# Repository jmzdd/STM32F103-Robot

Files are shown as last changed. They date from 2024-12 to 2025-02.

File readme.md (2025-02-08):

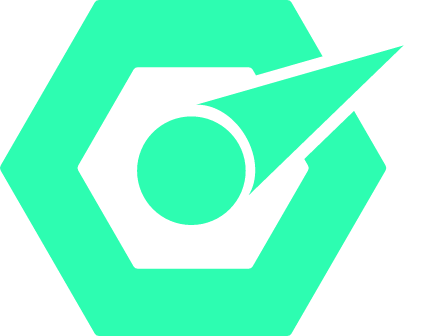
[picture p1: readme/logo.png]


# <p align="center">STM32F103-Robot</p>

<p align="center">
  
  
  
  
  
  
  
</p>

<p align="center" style="font-size: 24px; font-weight: bold;">🎉一个基于STM32F103C8T6的四足爬行机器人🎉</p>
<p align="center" style="font-size: 20px; font-weight: bold;">🚫项目仅供学习交流🚫</p>

## 一、项目介绍

&emsp;&emsp;本设计使用STM32F103C8T6作为主控，结合ESP32-CAM与MQTT，实现实时图像回传以及远程控制。

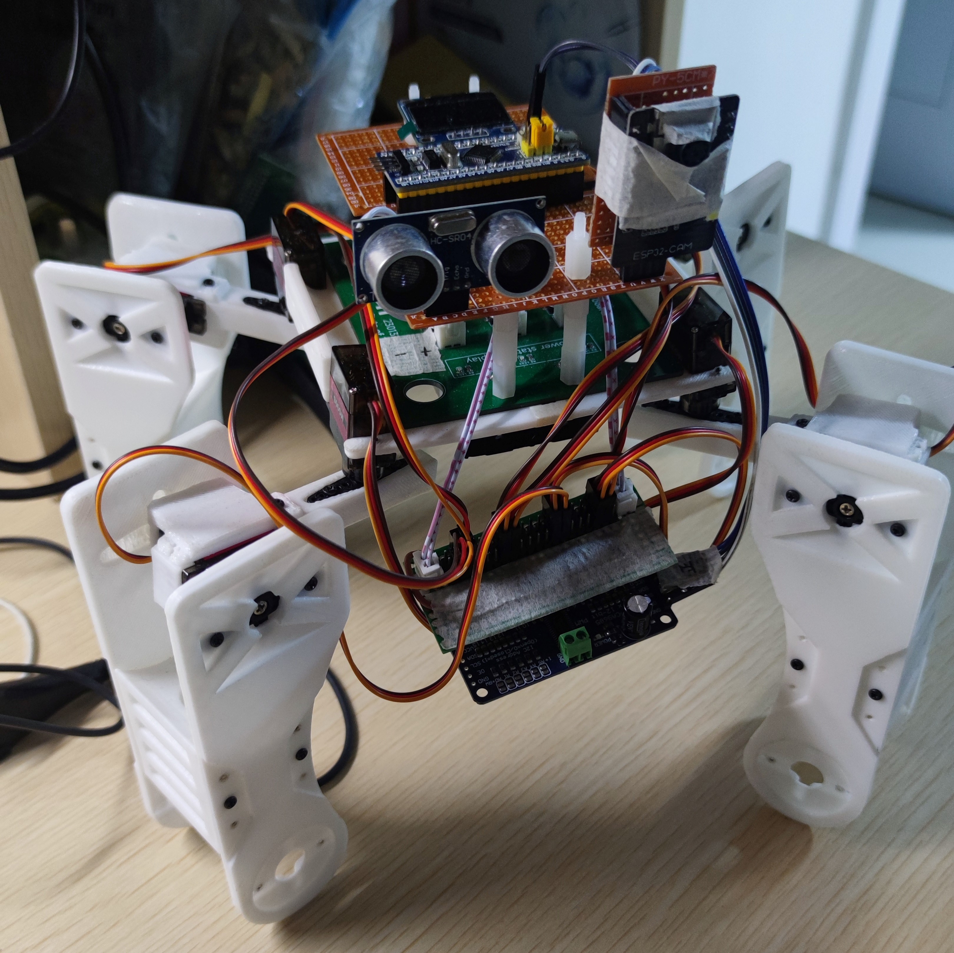
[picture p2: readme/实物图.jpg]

<p align="center">实物图</p>

&emsp;&emsp;在机器人的控制上使用了云端控制和本地控制两种方案。其中由Flet编写的移动端App能够通过MQTT协议与安装在服务器的EMQX进行通信，经云端传输的命令由ESP32-CAM接收后通过USART2传递给单片机，单片机就可以根据该命令控制模块，让机器人做出对应的动作。而ESP32-CAM拍摄的视频流则会实时上传至服务器，由服务器上部署的Nodejs Server接收后，通过网页呈现出来，至此实现了云端控制的全过程。

&emsp;&emsp;而本地控制则由Microdot来实现，在连接上由ESP32-CAM发出的热点之后，通过访问指定IP来访问本地控制面板。点击网页上的按钮就能够控制ESP32-CAM， ESP32-CAM通过串口向单片机发送命令。而由ESP32-CAM回传的图像流则会通过WIFI，实时显示在本地控制面板的上方。

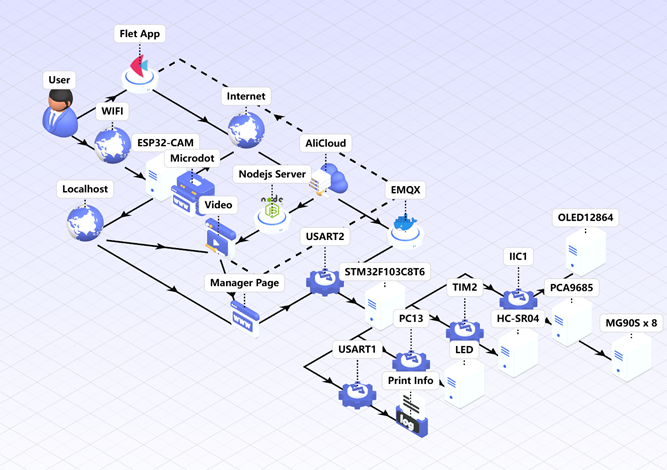
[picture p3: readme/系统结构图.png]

<p align="center">系统结构图</p>

&emsp;&emsp;仓库内包含了本项目所需的所有代码，其中还包括机器人的3D建模文件：

<div align="center">
  <table>
    <thead>
      <tr>
        <th style="text-align: left;">文件名</th>
        <th style="text-align: left;">说明</th>
      </tr>
    </thead>
    <tbody>
      <tr>
        <td style="text-align: left;">1、FreeCAD_Projects</td>
        <td style="text-align: left;">机器人3D建模工程文件</td>
      </tr>
      <tr>
        <td style="text-align: left;">2、HAL_C8T6</td>
        <td style="text-align: left;">开发STM32的工程文件</td>
      </tr>
      <tr>
        <td style="text-align: left;">3、Fletapp</td>
        <td style="text-align: left;">开发Flet应用的工程文件</td>
      </tr>
      <tr>
        <td style="text-align: left;">4、ESP32-CAM</td>
        <td style="text-align: left;">开发ESP32-CAM的Python代码以及前端代码</td>
      </tr>
      <tr>
        <td style="text-align: left;">5、CAM_Server</td>
        <td style="text-align: left;">服务器上负责ESP32-CAM图像接收的Nodejs代码</td>
      </tr>
      <tr>
        <td style="text-align: left;">6、Other</td>
        <td style="text-align: left;">包含Gerber文件和BOM表等文件</td>
      </tr>
    </tbody>
  </table>
</div>

## 二、项目设计过程

### 2.1 结构设计
&emsp;&emsp;四足爬行机器人的结构设计则使用了开源软件FreeCAD进行设计。结合MG90S舵机的尺寸，在腿部设计了凹槽与螺丝安装孔。机体中间预留电池安装孔，在关键位置还设计了螺丝孔，使结构更加牢固，方便后期的安装。

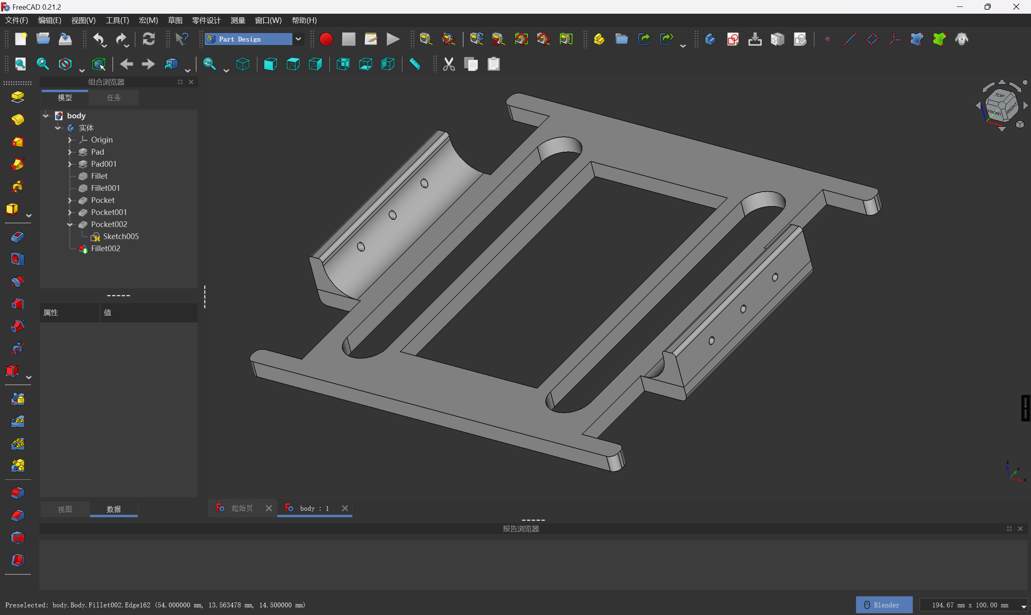
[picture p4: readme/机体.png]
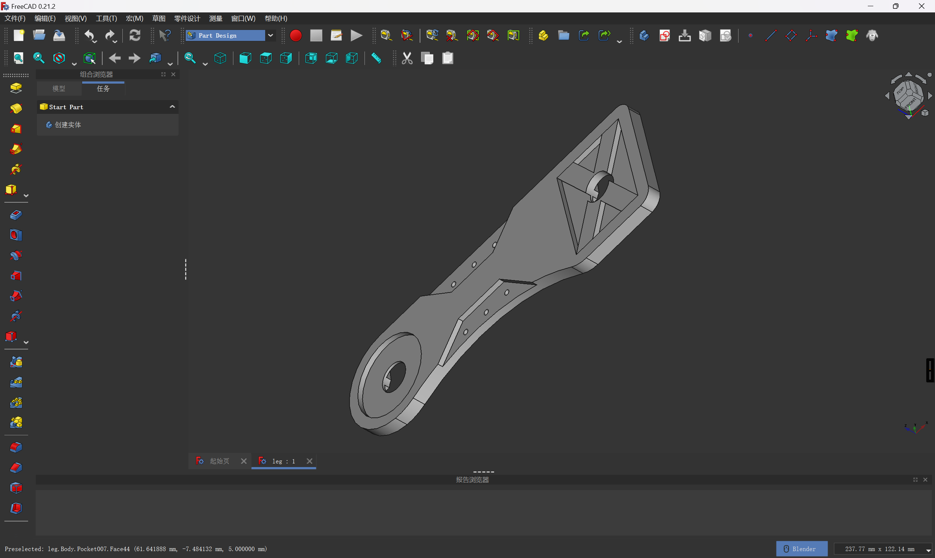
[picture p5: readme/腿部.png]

<p align="center">3D模型图</p>

&emsp;&emsp;建模完成后使用切片软件对模型进行切片，并将切片结果导入至3D打印机当中进行打印。填充密度为0.1mm，层厚0.2mm，挤出头温度设定为210℃。打印材料则选择了直径为1.75mm的PLA材料。电源板上预留了螺丝孔以安装尼龙柱，各个功能模块由万用板电路连接后通过尼龙柱堆叠在机体上方，方便快速装卸和调试。

### 2.2 电源设计

&emsp;&emsp;四足爬行机器人的电源模块选用了TI的TPS5430，在设计参考了[【电赛模块】TPS5430正负电源输出模块](https://oshwhub.com/quan-guo-dian-sai/dian-sai-mo-kuai-tps5430-fu-dian-yuan-shu-chu-mo-kuai)。电源模块上分别设计了三路电源，分别为舵机以及主控与功能模块进行供电。

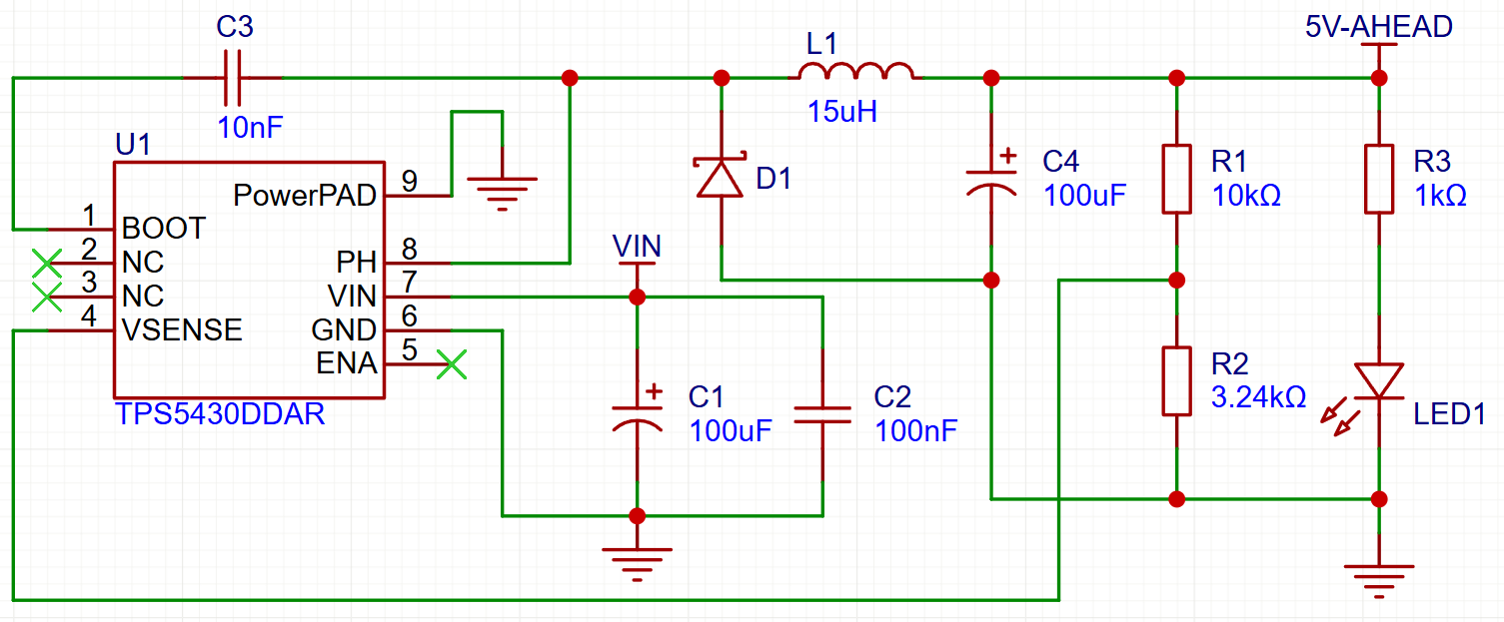
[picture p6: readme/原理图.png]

<p align="center">原理图</p>

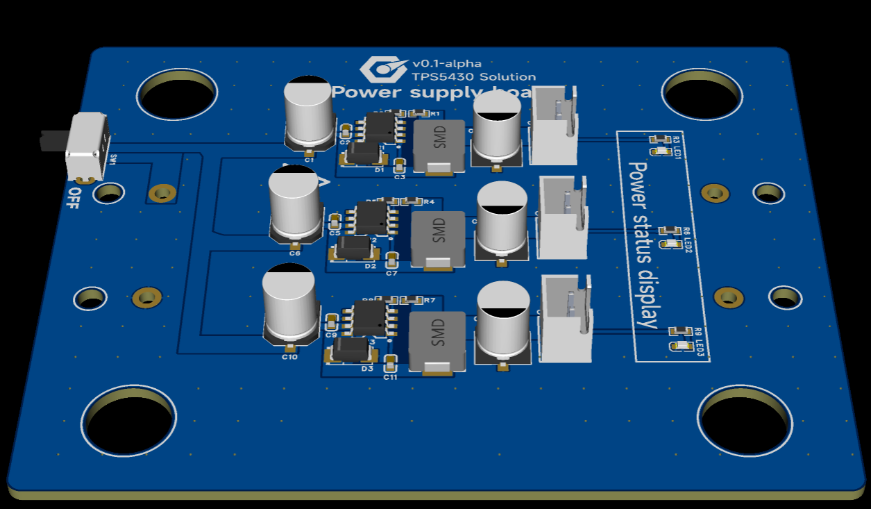
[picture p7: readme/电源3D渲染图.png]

<p align="center">电源板3D渲染图</p>

### 2.3 STM32F103C8T6的开发

&emsp;&emsp;在机器人上电后，首先初始化功能模块以及相关外设，同时初始化FreeRTOS，之后的任务就转交给FreeRTOS进行调度。在收到来自USART2的命令之前，单片机执行默认任务。在默认任务里，机器人始终保持停止状态，等待用户发送的命令。在USART2接收到命令后，单片机会进入串口中断程序，并在中断程序内判断该指令的具体含义，通过指令内容来执行对应的任务。

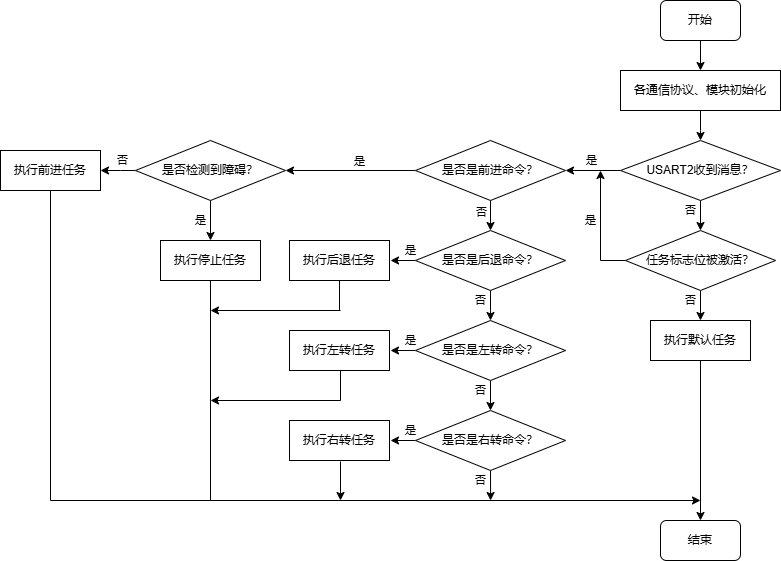
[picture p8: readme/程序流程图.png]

<p align="center">程序流程图</p>

&emsp;&emsp;当USART2收到来自ESP32-CAM发送的信息时，单片机会执行USART2的中断函数，在中断函数内，对接收到的信息进行判断。首先在代码中创建一个数组以设置缓冲区，结合HAL库函数将接收到的数据存在缓冲区当中，之后匹配缓冲区内的内容来判断是否是对应的命令。

&emsp;&emsp;在代码中先判断当前机器人所执行的任务是否是当前已经被激活的任务，如果是则直接跳过，避免了任务被重复激活而导致单片机死机。在判断任务没有被重复激活之后，通过事件位来触发机器人的动作任务。在动作任务被触发后，根据任务标志执行对应的任务内容。

&emsp;&emsp;匹配到对应的任务内容后，开始执行对应的代码。先在OLED上显示当前的任务状态，之后执行对应的动作函数，至此完成了任务流程。任务在被激活后会反复执行，直到被新的指令打断。

&emsp;&emsp;⚠注意：项目中还包括了STM32对OLED12864、HC-SR04超声波模块、PCA9685舵机驱动模块的驱动实现。关于驱动原理可以根据项目代码可看出，这里不再过多赘述，可自行下载项目代码查看。

### 2.4 ESP32-CAM开发

&emsp;&emsp;ESP32-CAM在烧录[MicoroPython固件](https://github.com/shariltumin/esp32-cam-micropython-2022)后使用[Arduino Lab for MicroPython](https://github.com/arduino/lab-micropython-editor)开发，相关的MicroPython固件也可在本仓库中获取。

&emsp;&emsp;[Microdot](https://github.com/miguelgrinberg/microdot)是一个极小的Python Web框架，专为资源受限的系统设计，例如微控制器以及嵌入式系统，适合运行在MicroPython之上。在本文的设计中，利用Microdot与ESP32-CAM支持WIFI的特性，在ESP32-CAM上搭建一个小型的Web服务器，实现用户与机器人之间的交互。

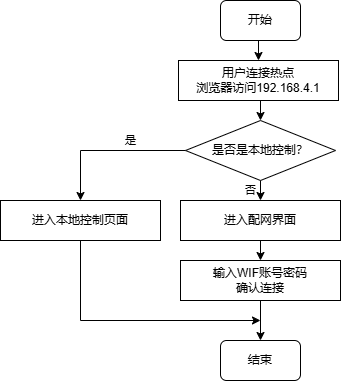
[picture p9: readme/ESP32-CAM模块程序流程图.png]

<p align="center">ESP32-CAM程序流程图</p>

&emsp;&emsp;ESP32-CAM在上电之后，会自行执行内部的程序。程序会在一开始初始化摄像头设备，并启动AP热点以等待用户连接。待用户连接到由ESP32-CAM发出的AP热点后，在浏览器中访问192.168.4.1，即可进入模式选择网页。这里的前端网页也是以文件的形式保存在ESP32-CAM当中的，因此整个连接过程完全在本地执行。

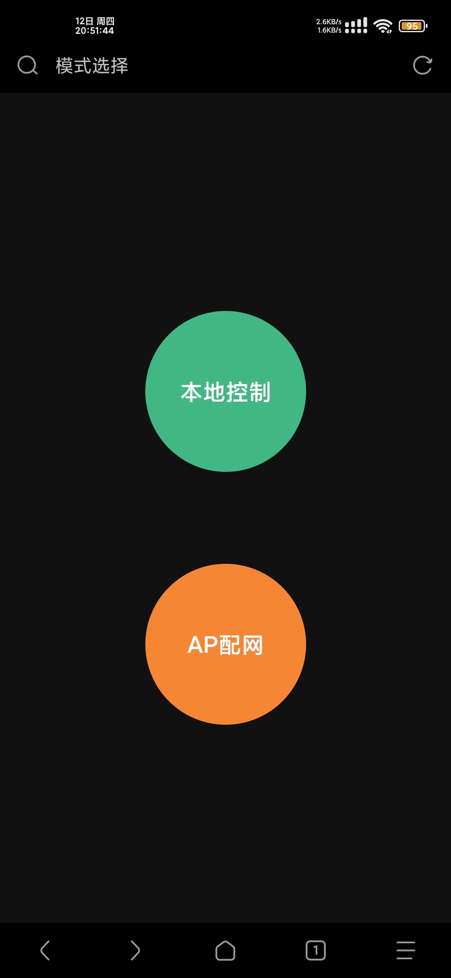
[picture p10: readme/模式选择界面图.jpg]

<p align="center">“模式选择”界面</p>

&emsp;&emsp;以本地控制为例，用户选择“本地控制”后，向ESP32-CAM发送Get请求。ESP32-CAM在接收到指令后，返回本地控制面板的网页。在本地控制网页当中就可以直接看到由ESP32-CAM拍摄的图像流画面。画面下方则为机器人的控制按钮，即前进、后退、左转、右转。当用户按下按钮后，按钮中间会出现信息提示，告诉用户当前按钮按下的功能以及按钮的状态。

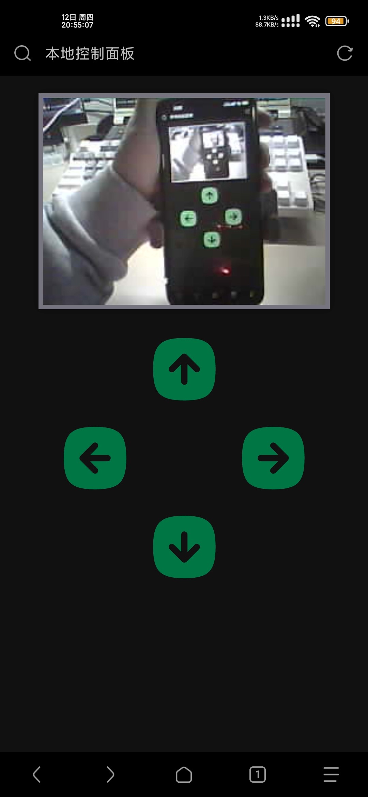
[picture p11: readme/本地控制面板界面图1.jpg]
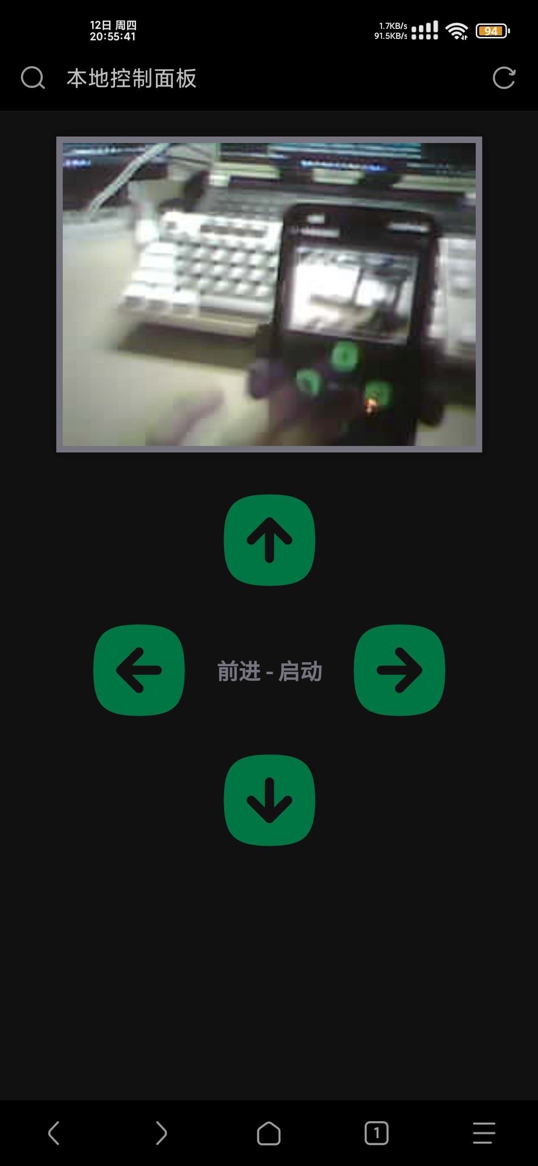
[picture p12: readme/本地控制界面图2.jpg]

<p align="center">“本地控制面板”界面</p>

&emsp;&emsp;在用户按下按钮后，同样会以Get请求的形式向ESP32-CAM发送命令，ESP32-CAM在接收到指令后，直接在串口输出命令，同时串口连接在STM32的USART2上。至此实现了用户对机器人的控制。

&emsp;&emsp;若用户选择的是AP配网，同样是以get请求的方式向ESP32-CAM发送数据，ESP32-CAM则向用户返回配网页面。在配网页面内，用户则需要输入WIFI名称和密码。由于ESP32-CAM只支持2.4G，因此用户在连接时需要注意连接的WIFI频段是否是2.4GHz的。

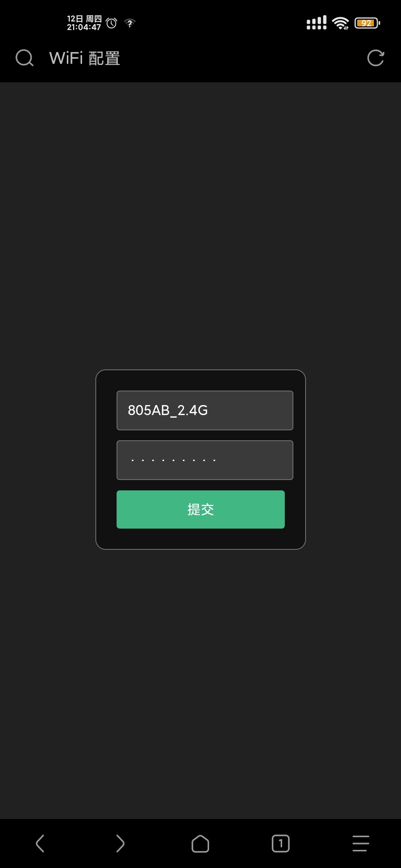
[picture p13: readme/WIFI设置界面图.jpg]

<p align="center">“WIFI设置”界面</p>

&emsp;&emsp;在用户提交信息之后，跳转至确认界面，这一设计为用户提供了一个修改的机会，如果之前填写的信息有误，用户可返回修改，若信息确认无误，则点击确认按钮提交至ESP32-CAM。

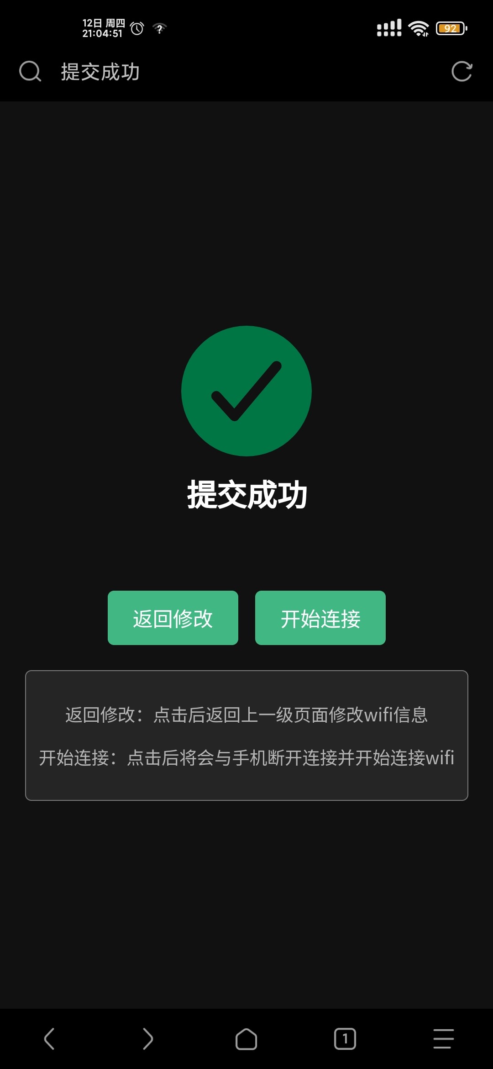
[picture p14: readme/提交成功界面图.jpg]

<p align="center">“提交成功”界面</p>

&emsp;&emsp;在ESP32-CAM接收到来自用户侧发送的WIFI信息后，则执行连接WIFI热点的代码，在连接WIFI的同时断开与用户的连接，同时连接至在代码中已经设置好的MQTT服务器，至此完成本地AP配网以及云端连接的流程。

&emsp;&emsp;在机器人上电后，首先初始化功能模块以及相关外设，同时初始化FreeRTOS，之后的任务就转交给FreeRTOS进行调度。在收到来自USART2的命令之前，单片机执行默认任务。在默认任务里，机器人始终保持停止状态，等待用户发送的命令。在USART2接收到命令后，单片机会进入串口中断程序，并在中断程序内判断该指令的具体含义，通过指令内容来执行对应的任务。

### 2.5 Flet应用开发

&emsp;&emsp;[Flet](https://github.com/flet-dev/flet)是一种基于Python的应用框架，允许开发者使用Python语言构建Web、桌面以及移动端应用程序，其灵感源于Google的Flutter。Flet的设计非常轻量，并且支持多种平台，具有一套代码多端使用的跨平台特性。基于Python语言构建使得应用程序更容易维护，同时社区提供了丰富的控件，可以轻松构建用户界面。

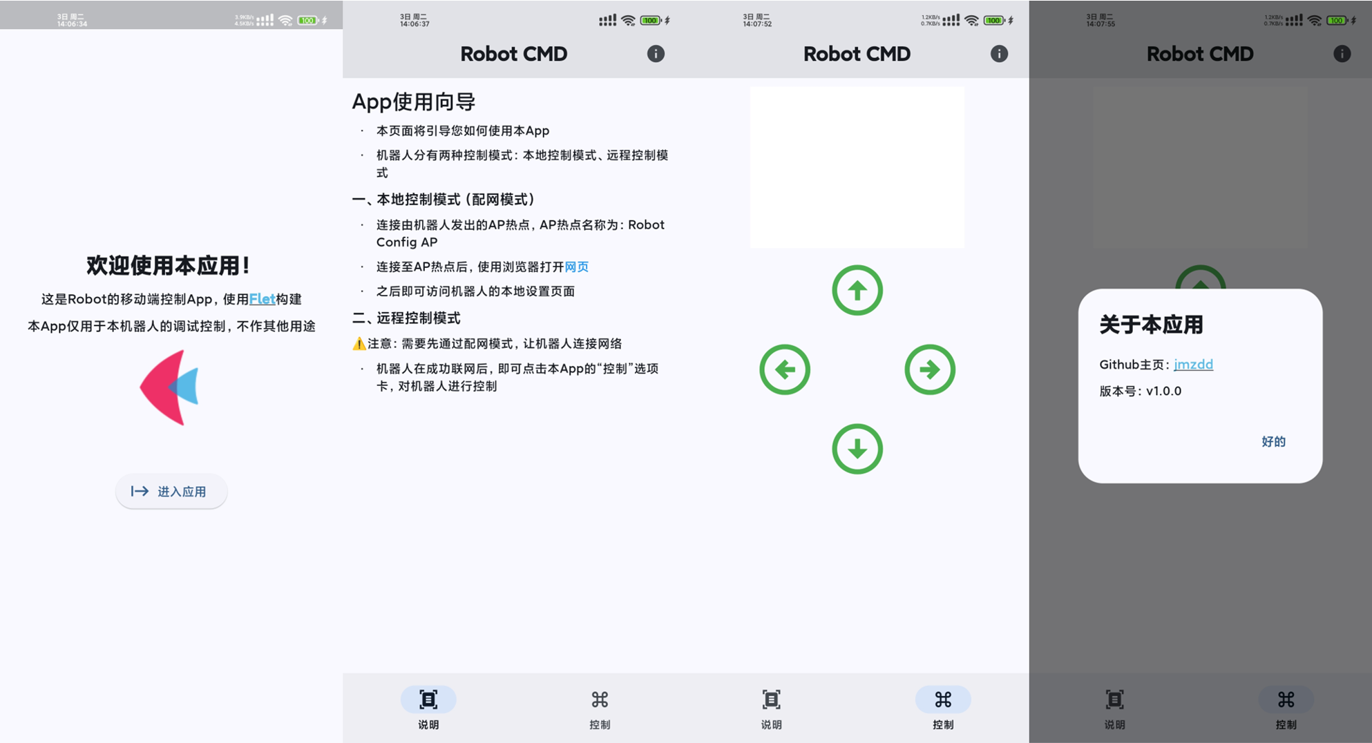
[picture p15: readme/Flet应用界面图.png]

<p align="center">Flet应用界面</p>

&emsp;&emsp;App主要分为“说明”页面与“控制”页面两个部分。“说明”页面的作用是向用户简要介绍App的使用方法，包括机器人的控制方法以及配网流程。“控制”页面则为用户提供控制界面，同时将云端获取到的视频流在界面中显示。

&emsp;&emsp;当用户选择“控制”按钮后，App会按照程序中的设置，连接到设置好的IP地址、端口以及订阅的Topic，连接至EMQX服务器。页面中的视频则以WebView控件的形式，将网页上的图像流显示在页面当中。

&emsp;&emsp;当用户按下按钮后，App则通过网络，向EMQX平台发送命令，由于ESP32-CAM和App都连接到了服务器并且订阅了相同的Topic，因此在App发送信息的同时，ESP32-CAM也能从云服务器收到消息。在ESP32-CAM收到命令后，则通过串口，将命令转发至STM32，触发串口中断并执行对应的任务。至此完成由用户端经云服务到机器人的控制流程。

## 三、机器人步态规划

&emsp;&emsp;机器人行进动作可拆分为三个状态，这里以前进动作为例：

+ 动作①：机器人将左右前肢与身体平行，后肢与身体呈135°夹角，四只脚垂直于地面，为接下来迈步做准备。
+ 动作②：机器人的左前脚与右后脚同时抬高45°，之后左前肢与右后肢同时向前45°，最后左前脚与右后脚同时落下。
+ 动作③：机器人的左后脚与右前脚同时抬高45°，之后左后肢与右前肢同时向前迈出45°，左前肢与右后肢同时向后45°最后左后脚与右前脚同时落下。

&emsp;&emsp;通过不断重复动作组，机器人能够实现四肢往返交替前进，而后退动作则是前进动作的镜像。

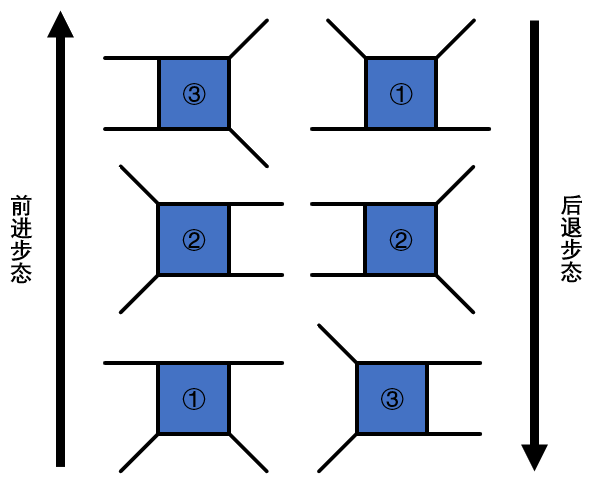
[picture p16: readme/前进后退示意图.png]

<p align="center">前进、后退步态示意图</p>

&emsp;&emsp;机器人的转体动作同样可分为三个部分，以左转动作为例：

+ 动作①：机器人将左右前肢与身体平行，后肢与身体呈135°夹角，四只脚垂直于地面，为接下来迈步做准备。
+ 动作②：左后脚与右前脚向上抬起45°，之后左后肢与右前肢先向逆时针移动45°后左后脚与右前脚落下。左前脚与右后脚抬起45°，右后肢逆时针移动45°后左前脚和右后脚落下。
+ 动作③：机器人将左后肢、右前肢和右后肢同时顺时针转45°，完成一次转体动作。

&emsp;&emsp;右转动作与左转相同，仅需将关节的旋转角度修改为逆时针即可。

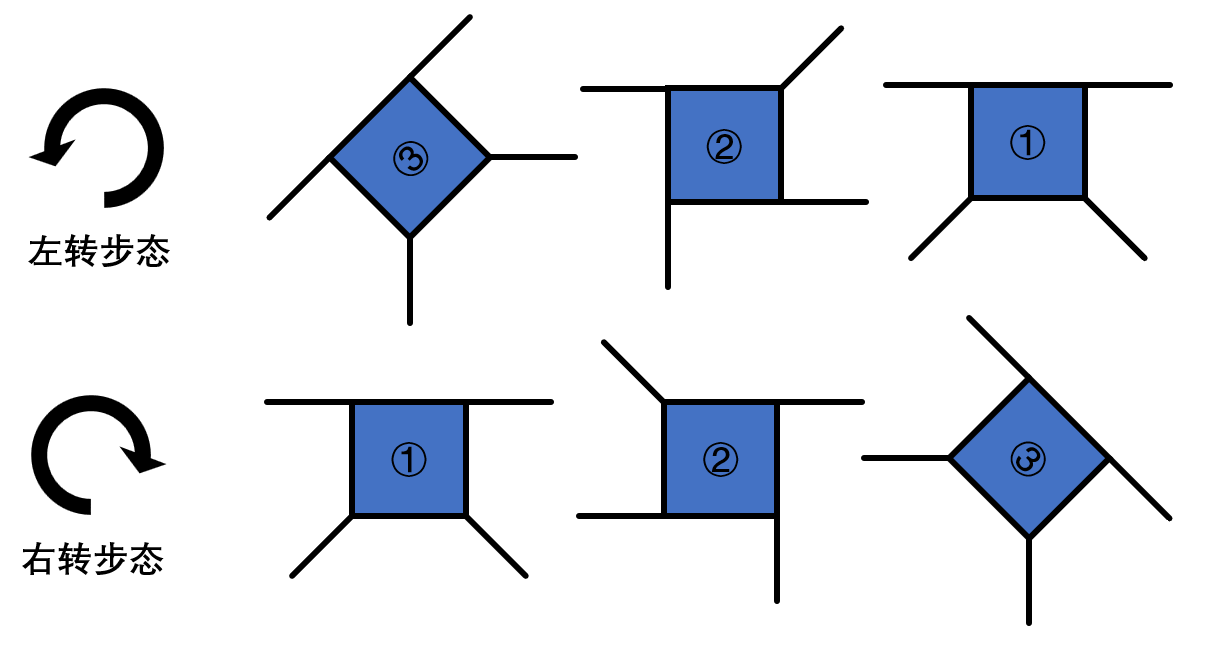
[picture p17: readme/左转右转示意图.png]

<p align="center">左转、右转步态示意图</p>

## 四、项目搭建及部署

### 4.1 MQTT服务器的部署以及服务器图像接收的配置

&emsp;&emsp;本项目使用EMQX作为MQTT服务器，其功能非常强大，可参考[EMQX官网](https://www.emqx.com/)进行部署。依托阿里云的轻量应用服务器，利用1panel linux运维面板快速安装应用。在1panel面板中找到应用市场，搜索EMQX并点击安装。服务器就会自动给执行命令，从Docker镜像仓库拉取镜像并自动部署。之后在阿里云的服务器管理界面开放对应的端口，可自行选择使用域名解析后访问。待安装完成后，直接在浏览器中访问域名即可进入EMQX的控制面板。

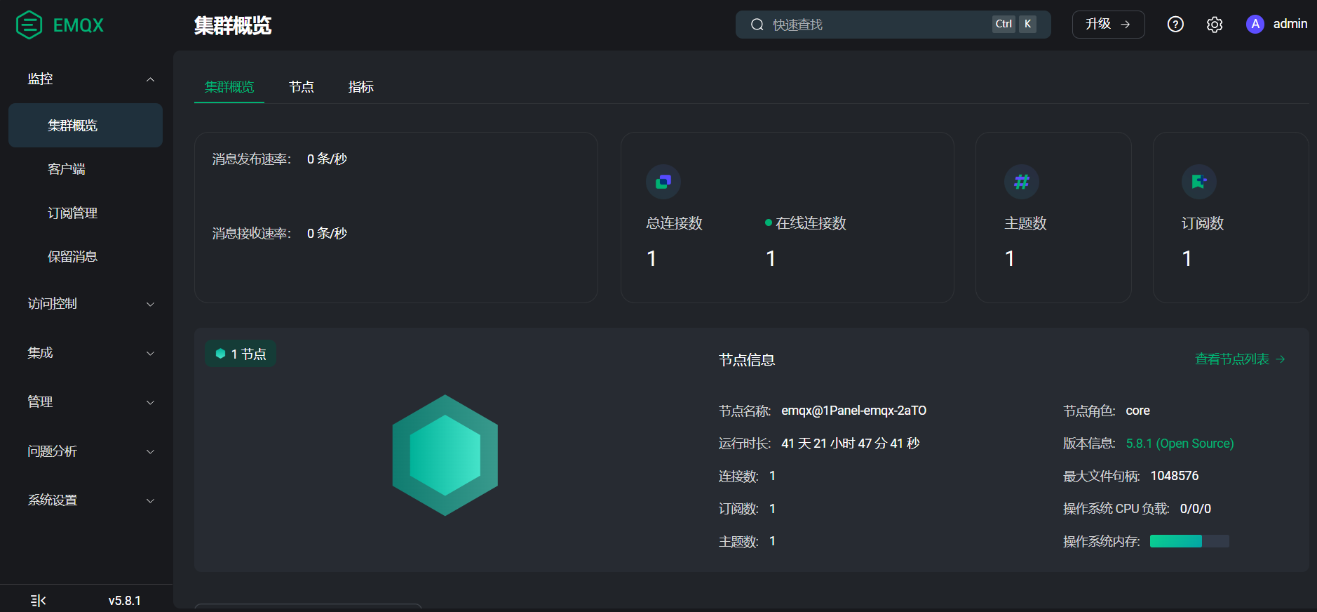
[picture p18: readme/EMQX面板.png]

<p align="center">EMQX面板</p>

&emsp;&emsp;同样是使用1panel linux运维面板，先将本仓库当中“CAM_Server”文件夹中的代码上传至服务器的文件目录当中。在运维面板的菜单中找到网站->运行环境，选择“node.js”,之后点击“创建运行环境”。

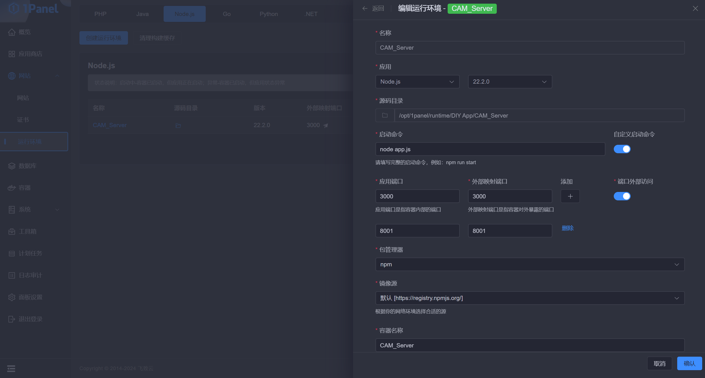
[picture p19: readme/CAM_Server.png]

<p align="center">创建运行环境</p>

&emsp;&emsp;记得到云服务器/运维面板的防火墙开启对应的端口哦！😊

### 4.2 STM32开发环境

&emsp;&emsp;STM32使用HAL库进行开发，用STMCubeMX建立基础工程，与CLion配合开发。关于环境的搭建教程网上已经有很多教程指导了，这里就不再赘述。clone本仓库代码后，直接使用Clion打开“HAL_C8T6”文件夹即可使用。

### 4.3 ESP32-CAM开发环境

&emsp;&emsp;下载完前文提到的Arduino Lab for MicroPython IDE之后，打开IDE并将ESP32-CAM连接电脑。在IDE内连接对应的串口，将本仓库代码中“ESP32-CAM”文件夹内的文件烧录到ESP-CAM当中。

&emsp;&emsp;在“main.py”当中，如下地方需要自行修改为自己的服务器信息：

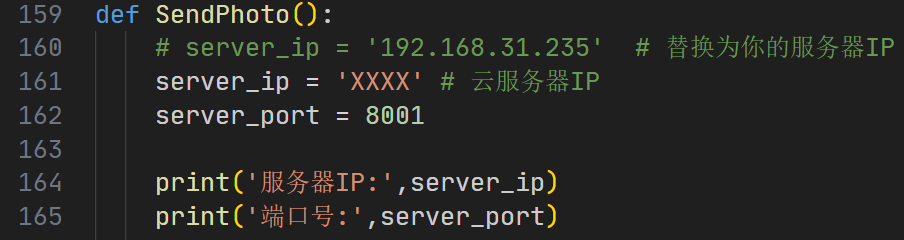
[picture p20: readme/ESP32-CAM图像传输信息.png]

<p align="center">接收图像的服务器信息</p>

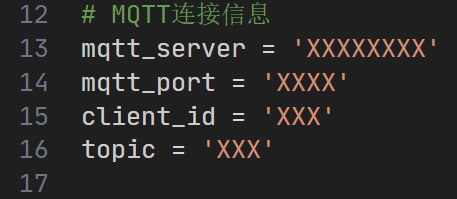
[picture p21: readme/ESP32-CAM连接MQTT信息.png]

<p align="center">MQTT服务器信息</p>

### 4.4 Flet应用开发环境

&emsp;&emsp;Flet应用由于使用Python语言，所以使用PyCharm IDE进行开发。Flet具体的环境搭建可以参考[Flet官方文档](https://flet.dev/docs/getting-started)。同样的，在clone本仓库的代码后，直接使用PyCharm IDE打开项目中的“Fletapp”文件夹即可使用。

&emsp;&emsp;在“mqtt.py”当中，如下地方需要自行修改为自己的服务器信息：

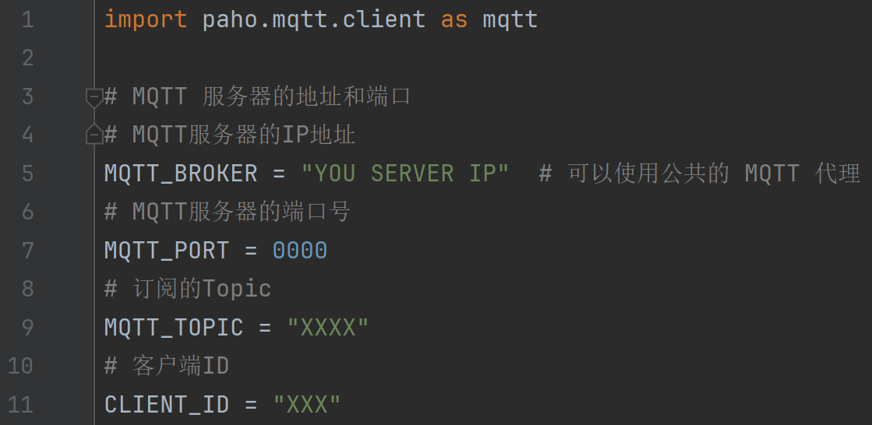
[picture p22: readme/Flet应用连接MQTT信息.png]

<p align="center">MQTT服务器信息</p>

&emsp;&emsp;在应用的开发过程中，由于编译出的APK文件一直不能够正常工作，因此就就尝试使用了Dev分支的SDK版本，以下是版本信息：

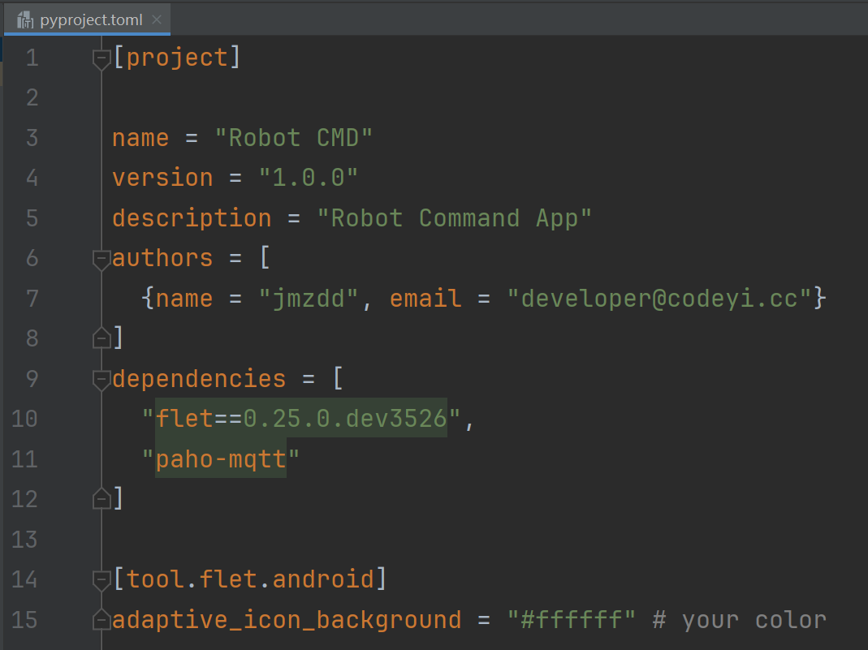
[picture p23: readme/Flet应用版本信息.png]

<p align="center">Flet应用版本信息</p>

### 4.5 模块接线图

&emsp;&emsp;在搞定软件后，将各个模块与STM32连接，以下是模块连接图：

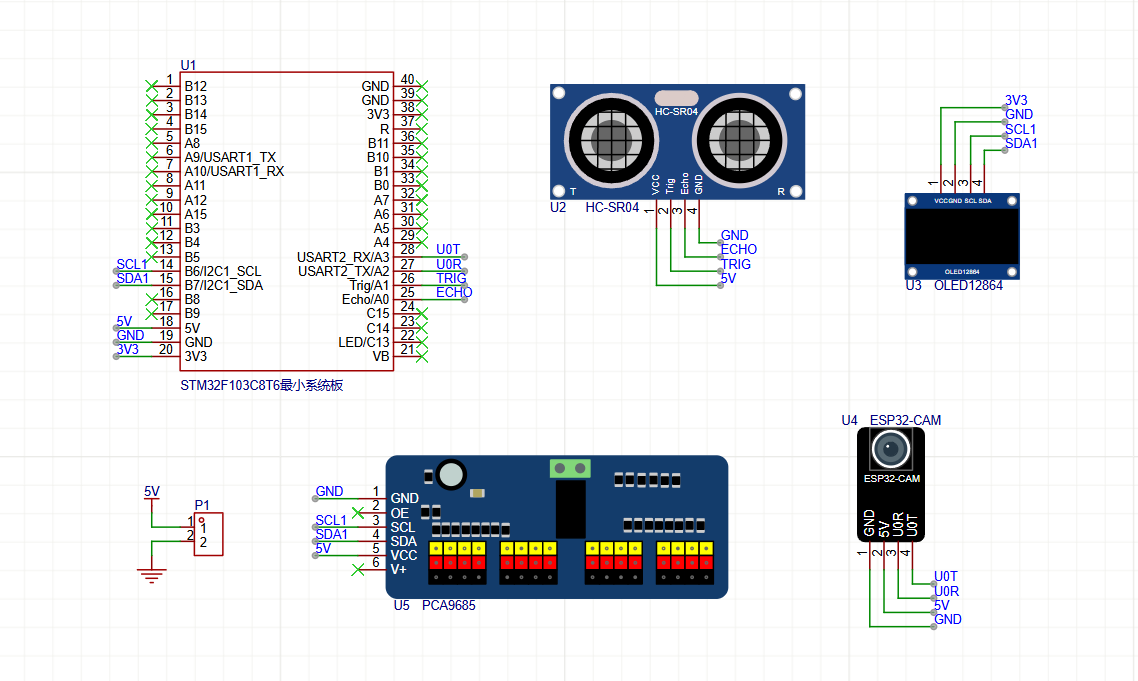
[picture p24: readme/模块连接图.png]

<p align="center">模块连接图</p>

&emsp;&emsp;至此，应该能够将这个小机器人造出来啦~😎

## 五、项目总结

+ 电源模块的设计仍然存在缺陷：虽然电源模块能够正常工作且输出电压，但是在设计过程当中仅仅考虑到了功能性，没有充分考虑到安全性。PCB电路的裸露容易导致线路因误触发生短路，会对电源模块乃至整个系统都造成安全威胁。可以考虑添加保险丝，可防止电源短路时产生的大电流导致的电路烧毁。同时还需要添加防反接/防倒灌二极管，以此来避免电源芯片的烧毁。
+ 舵机的选取以及机器人的结构与姿态问题：由于在设计之初没有考虑到电池的重量，导致在实际运行时MG90S无法轻松支撑起机器人的重量。在行进过程中，由于机器人的重心不稳定导致前进与后退的任务都不是按照正常的直线轨迹行进。也有可能是因为3D打印机的误差较大，导致实际打印出来的结构体都存在一定偏移，最终导致了机器人的重心不稳与受力不均。
+ App的优化：虽然App能够实现基础功能，但是仍然存在一系列的问题，例如App在使用完成后，必须清除缓存数据才能再次使用，否则打开之后屏幕会一直处于白屏状态，无法正常使用。同时App的控制界面没有实现自适应设备，一旦使用平板打开就会导致画面留有大量留白。在按下按钮后，按钮上方的画面也会随着页面同步刷新，影响使用。

<p align="center" style="font-size: 15px; font-weight: bold;">👇项目演示👇</p>

https://github.com/user-attachments/assets/f1a0bd48-f576-4248-8a84-5862ebdc9574

## 六、参考资料

+ [flet-dev/flet](https://github.com/flet-dev/flet)
+ [Alidong/PCA9685_STM32HAL](https://github.com/Alidong/PCA9685_STM32HAL)
+ [mokhwasomssi/stm32_hal_ssd1306](https://github.com/mokhwasomssi/stm32_hal_ssd1306)
+ [shariltumin/esp32-cam-micropython-2022](https://github.com/shariltumin/esp32-cam-micropython-2022)
+ [STM32入门教程-2023版 细致讲解 中文字幕](https://www.bilibili.com/video/BV1th411z7sn/?p=32)
+ [韦东山freeRTOS系列教程之【第八章】事件组(event group)](https://blog.csdn.net/thisway_diy/article/details/121532692)
+ [STM32系列(HAL库)——F103C8T6通过HC-SR04超声波模块实现测距](https://blog.csdn.net/lwb450921/article/details/123670786)

&emsp;&emsp;还有我以前的项目：

+ [jmzdd/Simple-Quadruped-Robot_Code](https://github.com/jmzdd/Simple-Quadruped-Robot_Code)
+ [jmzdd/Simple-Quadruped-Robot_Models](https://github.com/jmzdd/Simple-Quadruped-Robot_Models)

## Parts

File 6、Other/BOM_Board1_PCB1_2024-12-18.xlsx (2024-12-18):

No. | Quantity | Comment | Designator | Footprint | Value | Manufacturer Part | Manufacturer | Supplier Part | Supplier | 备注
1 | 1 | Battery | B1 | CB-18650-PC4 |  |  |  |  |  | 18650电池盒（约78mm*40mm）焊点距离：约78mm/19mm
2 | 6 | 100uF | C1,C4,C6,C8,C10,C12 | CAP-SMD_BD6.3-L6.6-W6.6-LS7.4-FD | 100uF | RVT100UF35V67RV0034 | KNSCHA(科尼盛) | C2836442 | LCSC
3 | 3 | 100nF | C2,C5,C9 | C0603 | 100nF | EMCP100W104M1GV001T | JOHANSON(约翰逊) | C17602234 | LCSC
4 | 3 | 10nF | C3,C7,C11 | C0603 | 10nF | 0603B103K500NT | FH(风华) | C57112 | LCSC
5 | 3 | ZX-XH2.54-2PZZ | CN1,CN2,CN3 | CONN-TH_2P-P2.50_HX25003-2A |  | ZX-XH2.54-2PZZ | Megastar(兆星) | C7429632 | LCSC
6 | 3 | B340A | D1,D2,D3 | SMA_L4.3-W2.6-LS5.1-RD |  | B340A | MDD(辰达半导体) | C64982 | LCSC
7 | 3 | 15uH | L1,L2,L3 | IND-SMD_L7.3-W6.8 | 15uH | MWSA0603S-150MT | Sunlord(顺络) | C408452 | LCSC
8 | 3 | XL-1608SURC-06 | LED1,LED2,LED3 | LED0603-RD_RED |  | XL-1608SURC-06 | XINGLIGHT(成兴光) | C965799 | LCSC
9 | 3 | 10kΩ | R1,R4,R7 | R0603 | 10kΩ | 0603WAF1002T5E | UNI-ROYAL(厚声) | C25804 | LCSC
10 | 3 | 3.24kΩ | R2,R5,R8 | R0603 | 3.24kΩ | 0603WAF3241T5E | UNI-ROYAL(厚声) | C22994 | LCSC
11 | 3 | 1kΩ | R3,R6,R9 | R0603 | 1kΩ | 0603WAF1001T5E | UNI-ROYAL(厚声) | C21190 | LCSC
12 | 1 | SK12D07VG3 | SW1 | SW-TH_SK12D07VG3 |  | SK12D07VG3 | SHOU HAN(首韩) | C431547 | LCSC
13 | 3 | TPS5430DDAR | U1,U2,U3 | ESOP-8_L4.9-W3.9-P1.27-LS6.0-TL-EP |  | TPS5430DDAR | TI(德州仪器) | C9864 | LCSC
18650可充电动力锂电池（3500毫安）*2
尼龙柱M3*10
M1.7*8自攻螺丝

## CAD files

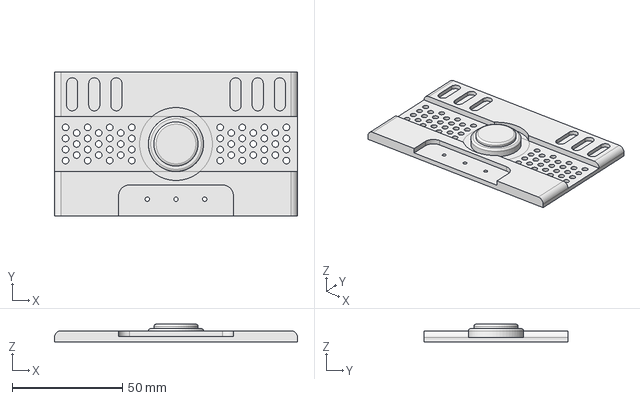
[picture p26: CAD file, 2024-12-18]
1、FreeCAD_Projects/body-port1.FCStd
110.0 x 65.0 x 8.00 mm

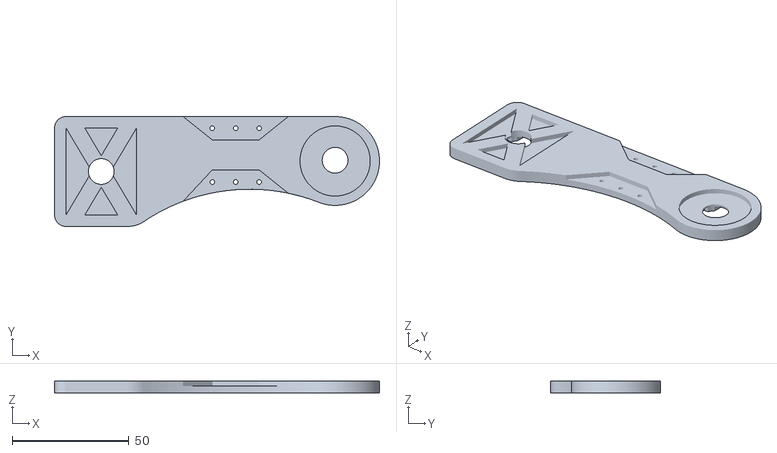
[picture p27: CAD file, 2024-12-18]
1、FreeCAD_Projects/models/leg-back.stl
139.0 x 47.0 x 5.00

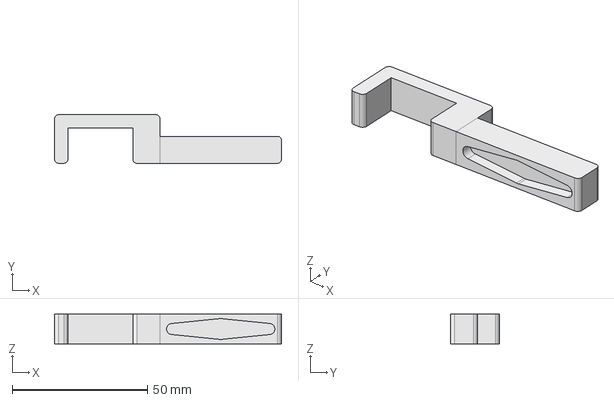
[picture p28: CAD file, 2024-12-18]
1、FreeCAD_Projects/leg-port2.FCStd
84.0 x 18.0 x 11.0 mm

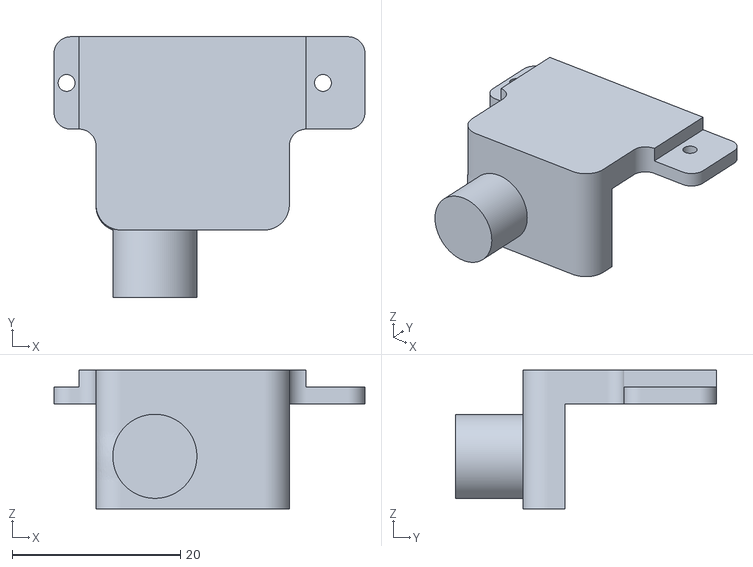
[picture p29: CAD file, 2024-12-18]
1、FreeCAD_Projects/models/foot-part3.stl
37.0 x 31.0 x 16.5

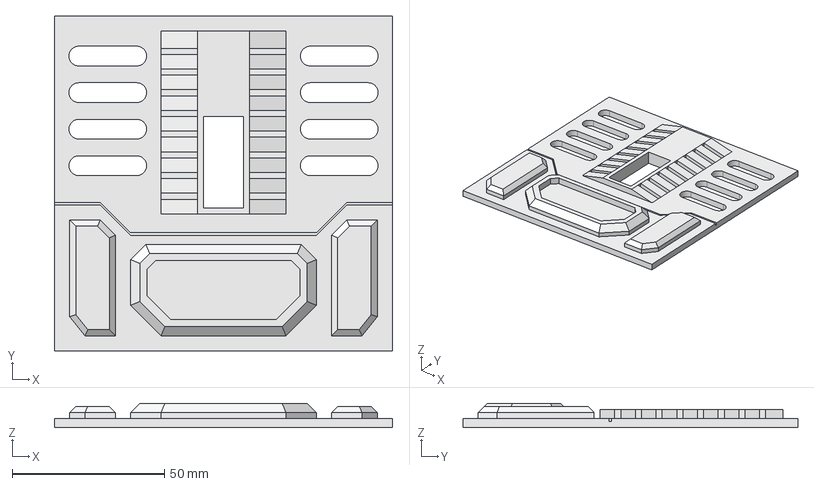
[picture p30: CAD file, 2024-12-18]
1、FreeCAD_Projects/body-port2.FCStd
111.0 x 110.0 x 8.00 mm

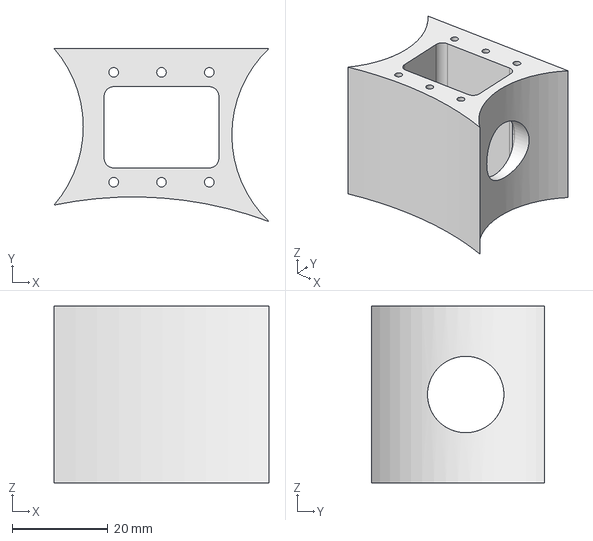
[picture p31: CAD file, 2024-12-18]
1、FreeCAD_Projects/leg-port1.FCStd
45.0 x 36.2 x 37.0 mm

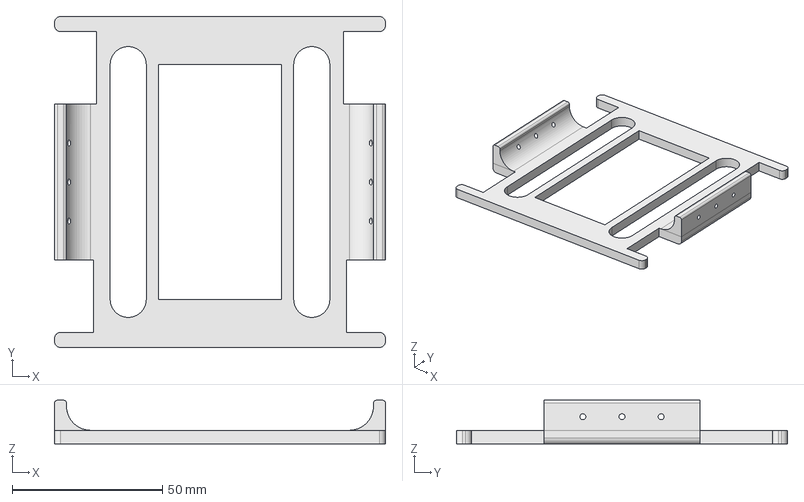
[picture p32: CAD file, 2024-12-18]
1、FreeCAD_Projects/body.FCStd
110.0 x 110.0 x 14.5 mm

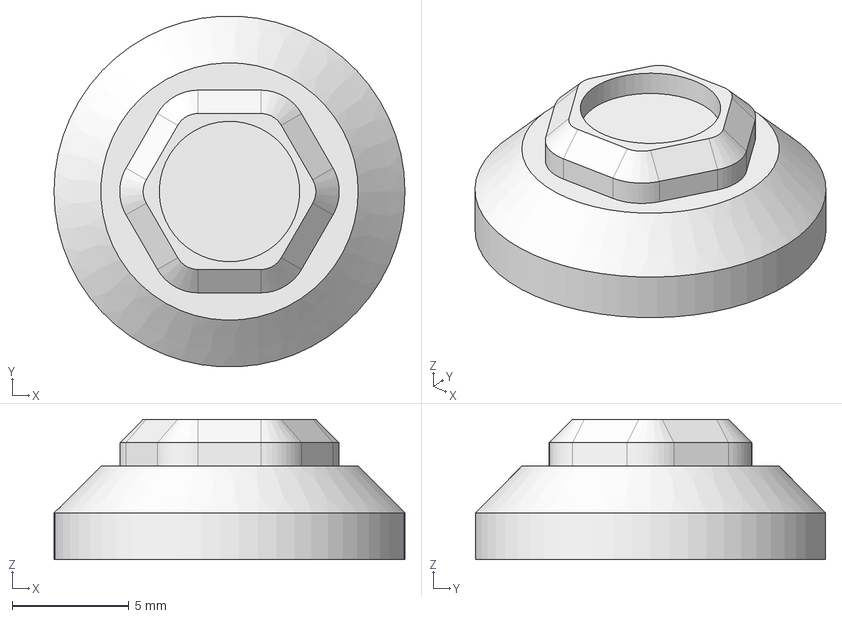
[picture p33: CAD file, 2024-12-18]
1、FreeCAD_Projects/foot-parts1.FCStd
15.0 x 15.0 x 6.00 mm

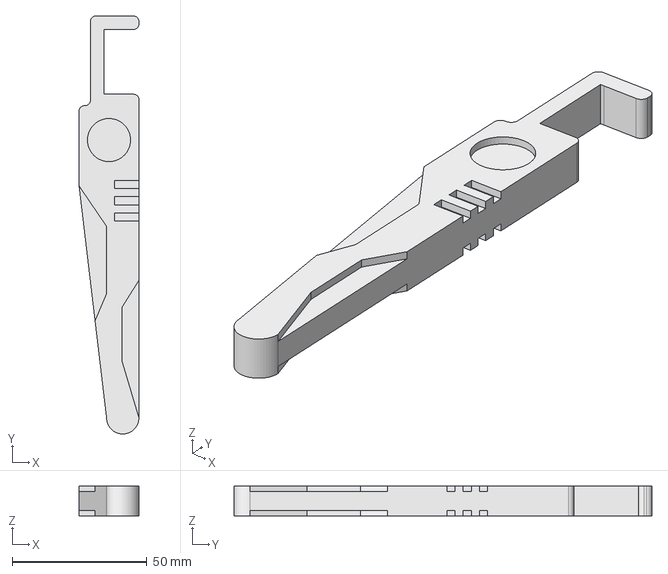
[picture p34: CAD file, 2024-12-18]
1、FreeCAD_Projects/foot.FCStd
22.2 x 155.0 x 11.0 mm

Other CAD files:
1、FreeCAD_Projects/models/leg-forward.stl
1、FreeCAD_Projects/leg.FCStd
1、FreeCAD_Projects/foot-part2.FCStd
1、FreeCAD_Projects/body-实体.stl
1、FreeCAD_Projects/models/foot-part2.stl
1、FreeCAD_Projects/models/foot-parts1.stl
1、FreeCAD_Projects/models/foot.stl
1、FreeCAD_Projects/models/leg-port1.stl
1、FreeCAD_Projects/models/leg-port2.stl

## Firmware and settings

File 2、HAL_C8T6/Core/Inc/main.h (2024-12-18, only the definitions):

#define LED_Pin GPIO_PIN_13
#define LED_GPIO_Port GPIOC
#define Echo_Pin GPIO_PIN_0
#define Echo_GPIO_Port GPIOA
#define Trig_Pin GPIO_PIN_1
#define Trig_GPIO_Port GPIOA

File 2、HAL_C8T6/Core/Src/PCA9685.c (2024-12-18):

/***************************************************
This is a library for our Adafruit 16-channel PWM & Servo driver

  Pick one up today in the adafruit shop!
  ------> http://www.adafruit.com/products/815

  These displays use I2C to communicate, 2 pins are required to
  interface. For Arduino UNOs, thats SCL -> Analog 5, SDA -> Analog 4

  Adafruit invests time and resources providing this open source code,
  please support Adafruit and open-source hardware by purchasing
  products from Adafruit!

  Written by Limor Fried/Ladyada for Adafruit Industries.
  BSD license, all text above must be included in any redistribution
 ****************************************************/

#include "PCA9685.h"
#include "math.h"
#include "i2c.h"
#include "cmsis_os.h"
#include "mpu6050.h"

uint16_t speed = 150;

uint8_t pca_read(uint8_t startAddress) {
    //Send address to start reading from.
    uint8_t tx[1];
    uint8_t buffer[1];
    tx[0]=startAddress;

    HAL_I2C_Master_Transmit(&hi2c1,pca_adrr, tx,1,10000);
    HAL_I2C_Master_Receive(&hi2c1,pca_adrr,buffer,1,10000);
    return buffer[0];
}

void pca_write(uint8_t startAddress, uint8_t buffer) {
    //Send address to start reading from.
    uint8_t tx[2];
    tx[0]=startAddress;
    tx[1]=buffer;
    HAL_I2C_Master_Transmit(&hi2c1,pca_adrr, tx,2,10000);

}

void pca_setfreq(float freq)//设置PWM频率
{
    uint8_t prescale,oldmode,newmode;
    double prescaleval;
    freq *= 0.92;
    prescaleval = 25000000;
    prescaleval /= 4096;
    prescaleval /= freq;
    prescaleval -= 1;
    prescale =floor(prescaleval + 0.5f);

    oldmode = pca_read(pca_mode1);

    newmode = (oldmode&0x7F) | 0x10; // sleep

    pca_write(pca_mode1, newmode); // go to sleep

    pca_write(pca_pre, prescale); // set the prescaler

    pca_write(pca_mode1, oldmode);
    HAL_Delay(2);

    pca_write(pca_mode1, oldmode | 0xa1);
}

void pca_setpwm(uint8_t num, uint32_t on, uint32_t off)
{
    pca_write(LED0_ON_L+4*num,on);
    pca_write(LED0_ON_H+4*num,on>>8);
    pca_write(LED0_OFF_L+4*num,off);
    pca_write(LED0_OFF_H+4*num,off>>8);
}
/*num:舵机PWM输出引脚0~15，on:PWM上升计数值0~4096,off:PWM下降计数值0~4096
一个PWM周期分成4096份，由0开始+1计数，计到on时跳变为高电平，继续计数到off时
跳变为低电平，直到计满4096重新开始。所以当on不等于0时可作延时,当on等于0时，
off/4096的值就是PWM的占空比。*/

/*
	函数作用：初始化舵机驱动板
	参数：1.PWM频率
		  2.初始化舵机角度
*/
void PCA_MG9XX_Init(float hz)
{
    pca_write(pca_mode1,0x0);
    pca_setfreq(hz);//设置PWM频率
    HAL_Delay(500);
}

/*
	函数作用：控制舵机转动；
	参数：1.输出端口，可选0~15；
		  2.起始角度，可选0~180；
		  3.结束角度，可选0~180；
		  4.模式选择，0 表示函数内无延时，调用时需要在函数后另外加延时函数，且不可调速，第五个参数可填任意值；
					  1 表示函数内有延时，调用时不需要在函数后另外加延时函数，且不可调速，第五个参数可填任意值；
					  2 表示速度可调，第五个参数表示速度值；
		  5.速度，可填大于 0 的任意值，填 1 时速度最快，数值越大，速度越小；
	注意事项：模式 0和1 的速度比模式 2 的最大速度大；
*/
void PCA_MG9XX(uint8_t num,uint8_t end_angle)
{
    uint32_t off=0;
    off=(uint32_t)(80+end_angle*2.2);
    pca_setpwm(num,0,off);
}

void SetAngle(uint8_t channel,uint8_t angle)
{
    uint32_t off=0;
    off=(uint32_t)(102.4*(1+angle/45));
    pca_setpwm(channel,0,off);
}

/* 功能函数 */
void advance_bot_init(void) {
    SetAngle(1,0);
    SetAngle(2,90);

    SetAngle(5,180);
    SetAngle(6,90);

    SetAngle(9,0);
    SetAngle(10,45);

    SetAngle(13,180);
    SetAngle(14,145);
}

void back_bot_init(void) {
    SetAngle(13,180);
    SetAngle(14,90);

    SetAngle(9,0);
    SetAngle(10,90);

    SetAngle(5,180);
    SetAngle(6,45);

    SetAngle(1,0);
    SetAngle(2,145);
}


void advance(void) {
  // 姿态初始化
  // advance_bot_init();
  // 第一组抬腿
  // SetAngle(1,45);
  // SetAngle(13,135);
  // osDelay(speed);
  // 第一组伸腿
  SetAngle(2,135);
  SetAngle(14,90);
  osDelay(speed);
  // 第一组下落同时开始回收
  SetAngle(1,0);
  SetAngle(13,180);
  osDelay(speed-30);
  // 第一组回收
  SetAngle(2,90);
  SetAngle(14,135);
  // 至此第一部分已经结束
  // 同时另一组开始抬腿
  SetAngle(5,135);
  SetAngle(9,45);
  osDelay(speed);
  // 第二组伸腿
  SetAngle(10,90);
  SetAngle(6,45);
  osDelay(speed);
  // 第二组下落同时开始回收
  SetAngle(5,180);
  SetAngle(9,0);
  osDelay(speed-30);
  // 第二组回收
  SetAngle(6,90);
  SetAngle(10,45);
  // 至此第二组已经结束
  // 同时第一组开始抬腿...
    SetAngle(1,45);
    SetAngle(13,135);
}

void back(void) {
  // 姿态初始化
  // back_bot_init();
  // 第一组抬腿
  // SetAngle(13,135);
  // SetAngle(1,45);
  // osDelay(speed);
  // 第一组伸腿
  SetAngle(14,135);
  SetAngle(2,90);
  osDelay(speed);
  // 第一组下落同时开始回收
  SetAngle(13,180);
  SetAngle(1,0);
  osDelay(speed-30);
  // 第一组回收
  SetAngle(14,90);
  SetAngle(2,145);
  // 至此第一部分已经结束
  // 同时另一组开始抬腿
  SetAngle(9,45);
  SetAngle(5,135);
  osDelay(speed);
  // 第二组伸腿
  SetAngle(10,45);
  SetAngle(6,90);
  osDelay(speed);
  // 第二组下落同时开始回收
  SetAngle(9,0);
  SetAngle(5,180);
  osDelay(speed-30);
  // 第二组回收
  SetAngle(10,90);
  SetAngle(6,45);
  // 至此第二组已经结束
  // 同时第一组开始抬腿...
  SetAngle(13,135);
  SetAngle(1,45);

}

void turn_left(void) {
  advance_bot_init();
  // 第一组抬腿
  SetAngle(1,45);
  SetAngle(13,135);
  osDelay(speed);
  // 第一组挪腿
  SetAngle(2,90);
  SetAngle(14,90);
  osDelay(speed);
  // 第一组下落同时准备开始回收
  SetAngle(1,0);
  SetAngle(13,180);
  // 至此第一部分已经结束
  // 同时另一组开始抬腿
  SetAngle(5,135);
  SetAngle(9,45);
  osDelay(speed);
  // 第二组挪腿
  SetAngle(6,45);
  SetAngle(10,0);
  osDelay(speed);
  // 第二组下落
  SetAngle(5,180);
  SetAngle(9,0);
  osDelay(speed);
  // 四足归位
  SetAngle(2,90);
  SetAngle(14,135);
  SetAngle(6,90);
  SetAngle(10,45);
}

void turn_right(void) {
  advance_bot_init();
  // 第一组抬腿
  SetAngle(5,135);
  SetAngle(9,45);
  osDelay(speed);
  // 第一组挪腿
  SetAngle(6,90);
  SetAngle(10,90);
  osDelay(speed);
  // 第一组下落同时准备开始回收
  SetAngle(5,180);
  SetAngle(9,0);
  // 至此第一部分已经结束
  // 同时另一组开始抬腿
  SetAngle(1,45);
  SetAngle(13,135);
  osDelay(speed);
  // 第二组挪腿
  SetAngle(2,135);
  SetAngle(14,180);
  osDelay(speed);
  // 第二组下落
  SetAngle(1,0);
  SetAngle(13,180);
  osDelay(speed);
  // 四足归位
  SetAngle(6,90);
  SetAngle(10,45);
  SetAngle(2,90);
  SetAngle(14,135);
}

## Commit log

2024-12-18 提交项目文件
    [BOM_Board1_PCB1_2024-12-18.xlsx, body-port1.FCStd, body-port2.FCStd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]
2024-12-18 提交项目演示视频
2024-12-19 移除视频

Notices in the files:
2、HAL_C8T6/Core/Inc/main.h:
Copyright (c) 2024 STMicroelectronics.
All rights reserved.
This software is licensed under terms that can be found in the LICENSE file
